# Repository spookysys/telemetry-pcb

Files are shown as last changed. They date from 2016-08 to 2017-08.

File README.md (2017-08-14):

# A brain for my rocket

## Features 

* Arduino-compatible
* Adafruit Feather M0 firmware and pinout
* Small size - fits the smallest model rockets (e.g. 26mm diameter)
* Fairly powerful MCU (Atmel ARM M0 at 32MHz)
* GSM/GPRS for telemetry (SIM868)
* GPS for positioning (SIM868)
* 9-DOF Inertial Motion Unit (MPU-9259)
* Altimeter (BMP-280)
* MicroSD for logging
* Integrated usb-port, lipo-charger and power switch

## Adafruit Feather compatibility

* Same pinout as Adafruit Feather M0. An on-board component interfers with D5 (see note).
* MicroSD wired similar to Adalogger M0, but chip-select is on D7 not D4
* Voltage is 3.0 instead of 3.3
* I2C pull-ups are present

Note: If you don't need hardware handshaking on the GSM UART, the D5 pin can be freed up by cutting JP2 on the back of the board.

## Status

Testing in progress

## Credit

Design derived from Adafruit M0 Feather Proto and Adalogger

Adafruit invests time and resources providing this open source design, 
please support Adafruit and open-source hardware by purchasing 
products from Adafruit!

Creative Commons Attribution, Share-Alike license, check license.txt for more information
All text above must be included in any redistribution

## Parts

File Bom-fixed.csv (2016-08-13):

Part/Designator | Manufacture Part Number/Seeed SKU | Quantity
C12 | 302010001 | 1
C2, C4 | 302010143 | 2
C15 | 302010000 | 1
C10 | 302010006 | 1
C9,C11,C13,C19,C22,C24 | 302010037 | 6
C1,C7,C14 | 302010139 | 3
C3,C5,C6,C8,C17,C20,C21,C23 | 302010103 | 8
C16,C18 | 302020015 | 2
GPS_ANT,GSM_ANT | 320110048 | 2
L1 | 304090046 | 1
L2 | 304090057 | 1
L3 | 304090061 | 1
R2,R6,R7 | 301010291 | 3
R8 | 301010293 | 1
R4, R5 | 301010010 | 2
R1 | 301010089 | 1
R3, R9 | 301010456 | 2
SW1 | 311020047 | 1
X1 | 320110026 | 1
X2 | 306010055 | 1
X3 | 320010000 | 1
D1 | 304020034 | 1
D2 | MMSZ5231BT1G | 1
D3 | SMF05CT2G | 1
U1 | ATSAMD21G18A-M | 1
U2 | SPX3819M5-L-3-0 | 1
U3 | MCP73831T-2ACI/OT | 1
U4 | MPU-9250 | 1
U5 | SIM868 | 1
X4 | 104239-1430 | 1
U6 | BMP280 | 1

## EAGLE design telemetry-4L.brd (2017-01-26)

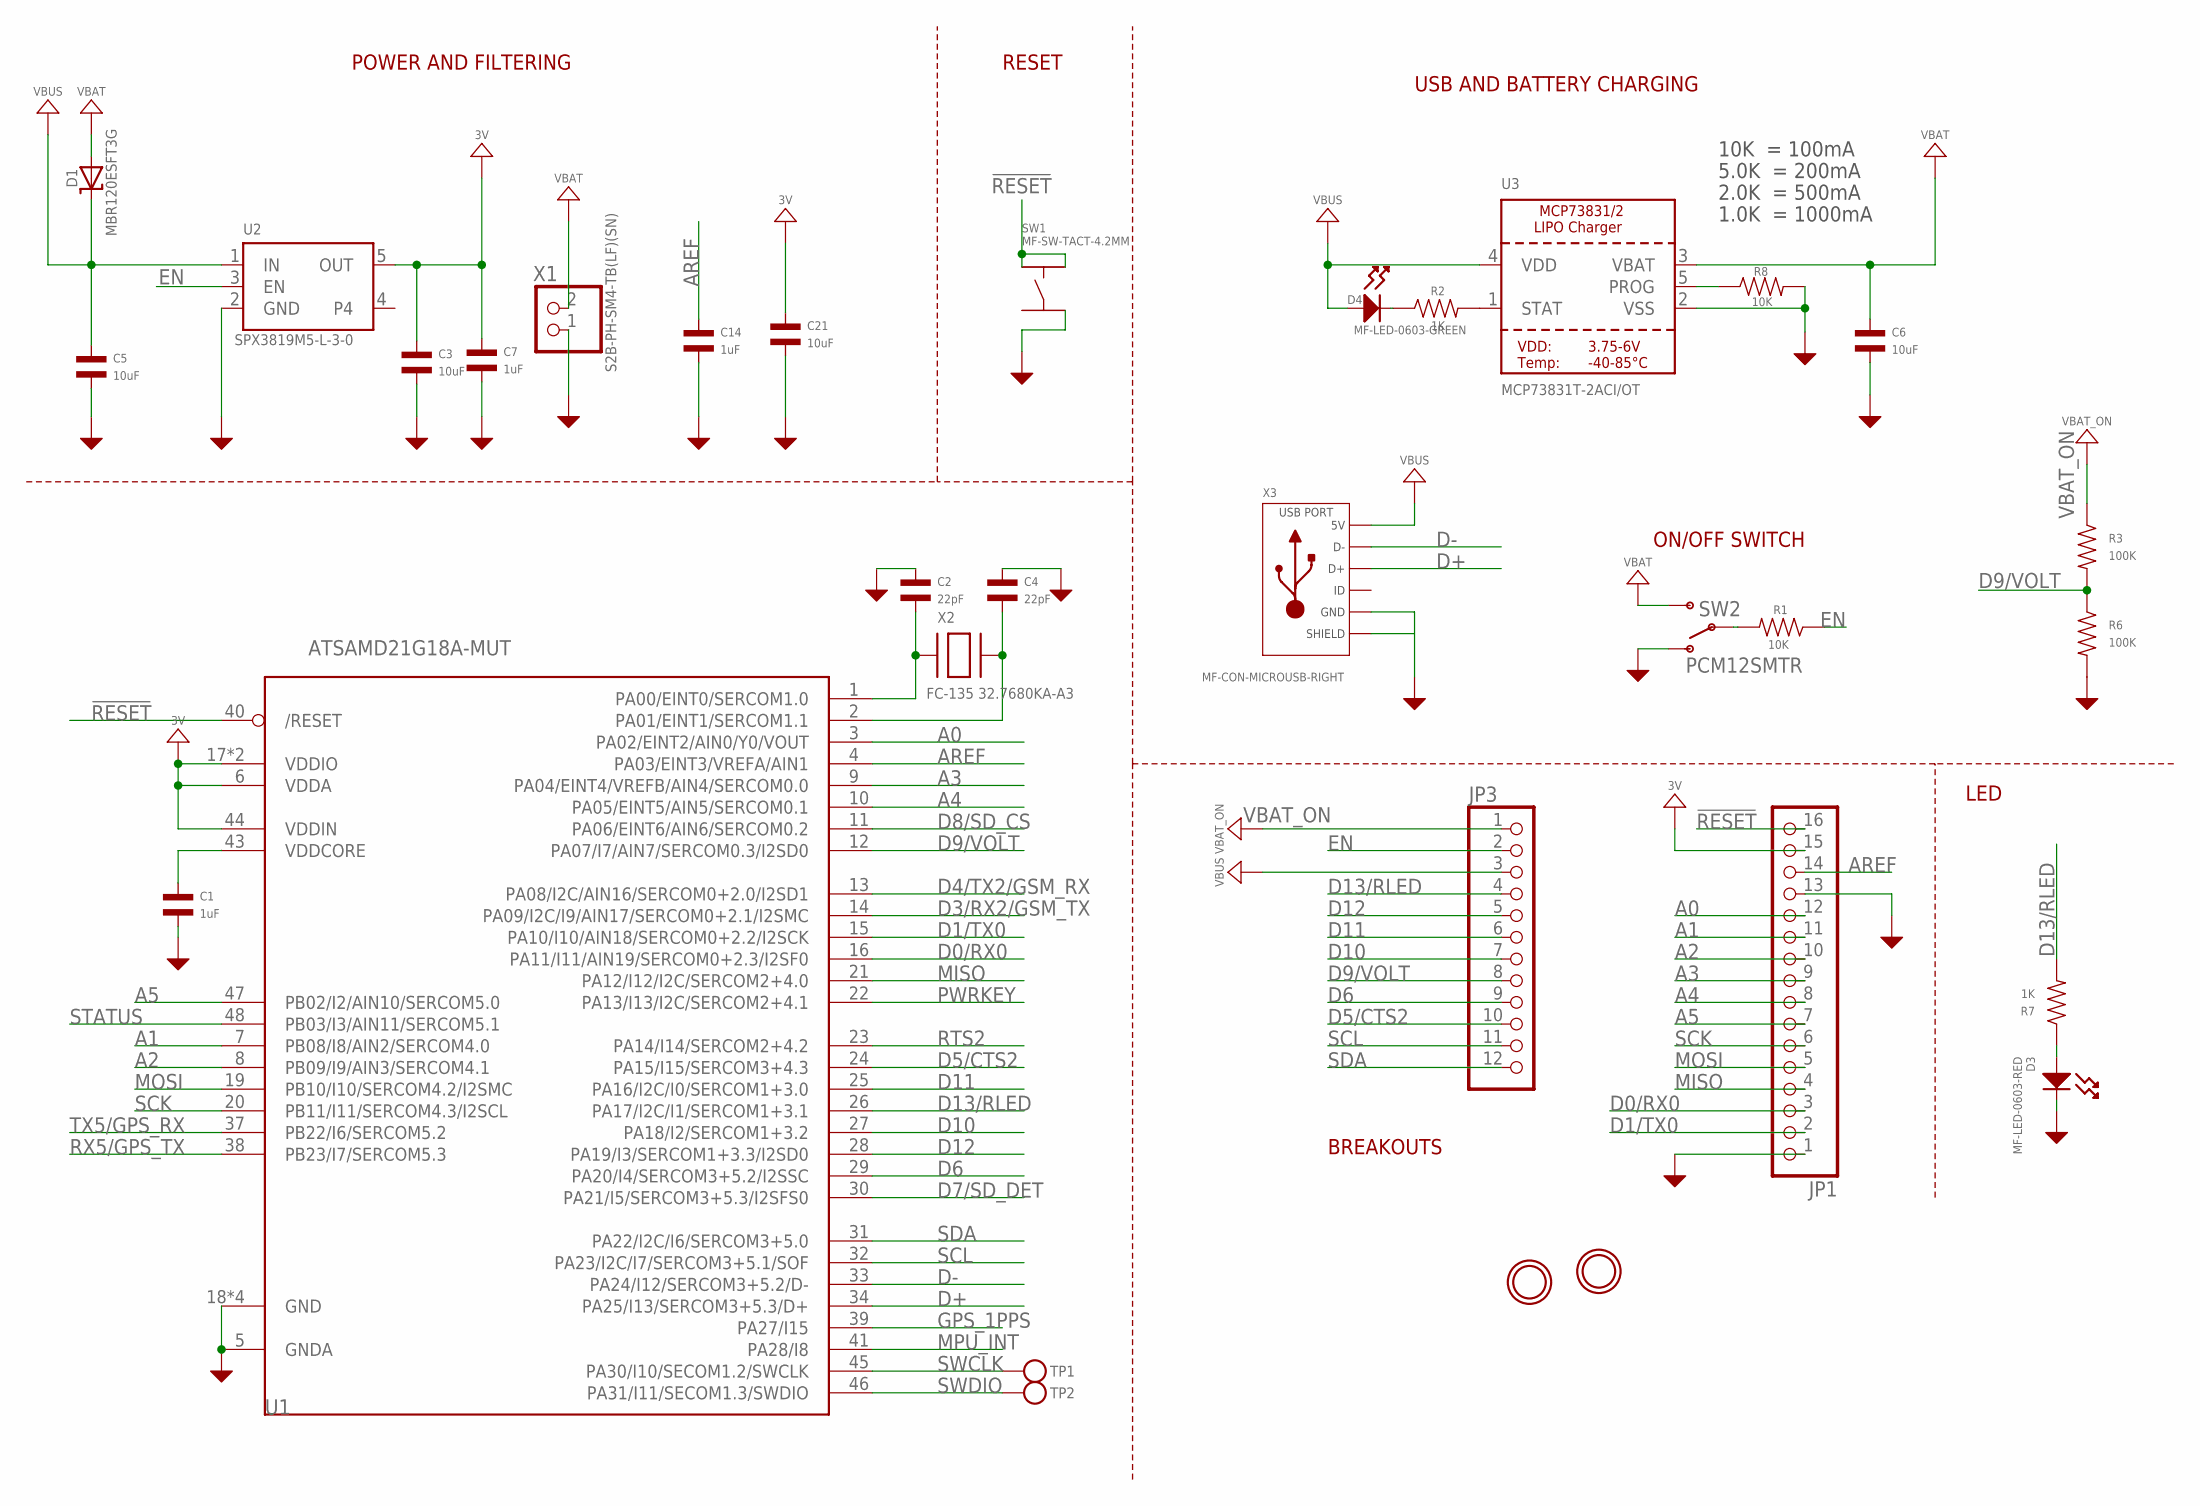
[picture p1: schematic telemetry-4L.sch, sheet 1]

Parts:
C1, C7, C14: 1uF; C0402
C2, C4: 22pF; C0402
C3, C5, C6, C21: 10uF; C0603; MPN GRM188R60J106ME47D
D1: MBR120ESFT3G; SOD-123
D3: MF-LED-0603-RED; LED0603
D4: MF-LED-0603-GREEN; LED0603
JP1: HEADER-1X16ROUND; 1X16_ROUND
JP3: HEADER-1X12; 1X12_ROUND
R1, R8: 10K; R0402
R2, R7: 1K; R0402
R3, R6: 100K; R0402
SW1: MF-SW-TACT-4.2MM; TACT4.2MM
SW2: PCM12SMTR; KPS-1290
TP1, TP2: TESTPOINTROUND1.5MM; TESTPOINT_ROUND_1.5MM
U1: ATSAMD21G18A-MUT; TQFN48_7MM
U2: SPX3819M5-L-3-0; SOT23-5
U3: MCP73831T-2ACI/OT; SOT23-5
U$31, U$32: MOUNTINGHOLE2.5; MOUNTINGHOLE_2.5_PLATED
X1: S2B-PH-SM4-TB(LF)(SN); JSTPH2
X2: FC-135 32.7680KA-A3; XTAL3215
X3: MF-CON-MICROUSB-RIGHT; MICROUSB-RIGHT

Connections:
!RESET: JP1.16, SW1.P$1, SW1.P$2, U1.40 (/RESET)
+3V: C3.P$1, C7.P$1, C21.P$1, JP1.15, U1.6 (VDDA), U1.17 (VDDIO), U1.36 (VDDIO), U1.44 (VDDIN), U2.5 (OUT); also elsewhere on the board
A0: JP1.12, U1.3 (PA02/EINT2/AIN0/Y0/VOUT)
A1: JP1.11, U1.7 (PB08/I8/AIN2/SERCOM4.0)
A2: JP1.10, U1.8 (PB09/I9/AIN3/SERCOM4.1)
A3: JP1.9, U1.9 (PA04/EINT4/VREFB/AIN4/SERCOM0.0)
A4: JP1.8, U1.10 (PA05/EINT5/AIN5/SERCOM0.1)
A5: JP1.7, U1.47 (PB02/I2/AIN10/SERCOM5.0)
AREF: C14.P$1, JP1.14, U1.4 (PA03/EINT3/VREFA/AIN1)
D0/RX0: JP1.3, U1.16 (PA11/I11/AIN19/SERCOM0+2.3/I2SF0)
D1/TX0: JP1.2, U1.15 (PA10/I10/AIN18/SERCOM0+2.2/I2SCK)
D3/RX2/GSM_TX: U1.14 (PA09/I2C/I9/AIN17/SERCOM0+2.1/I2SMC); also elsewhere on the board
D4/TX2/GSM_RX: U1.13 (PA08/I2C/AIN16/SERCOM0+2.0/I2SD1); also elsewhere on the board
D5/CTS2: JP3.10, U1.24 (PA15/I15/SERCOM3+4.3); also elsewhere on the board
D6: JP3.9, U1.29 (PA20/I4/SERCOM3+5.2/I2SSC)
D7/SD_DET: U1.30 (PA21/I5/SERCOM3+5.3/I2SFS0); also elsewhere on the board
D8/SD_CS: U1.11 (PA06/EINT6/AIN6/SERCOM0.2); also elsewhere on the board
D9/VOLT: JP3.8, R3.P$2, R6.P$1, U1.12 (PA07/I7/AIN7/SERCOM0.3/I2SD0)
D10: JP3.7, U1.27 (PA18/I2/SERCOM1+3.2)
D11: JP3.6, U1.25 (PA16/I2C/I0/SERCOM1+3.0)
D12: JP3.5, U1.28 (PA19/I3/SERCOM1+3.3/I2SD0)
D13/RLED: JP3.4, R7.P$2, U1.26 (PA17/I2C/I1/SERCOM1+3.1)
D+: U1.34 (PA25/I13/SERCOM3+5.3/D+), X3.3 (D+)
D-: U1.33 (PA24/I12/SERCOM3+5.2/D-), X3.2 (D-)
EN: JP3.2, R1.P$1, U2.3 (EN); also elsewhere on the board
GND: C1.P$2, C2.P$1, C3.P$2, C4.P$1, C5.P$2, C6.P$2, C7.P$2, C14.P$2, C21.P$2, D3.CATHODE, JP1.1, JP1.13, R6.P$2, R8.P$2, SW1.P$4, SW2.O, U1.5 (GNDA), U1.18 (GND), U1.35 (GND), U1.42 (GND), U1.THERMAL (GND), U2.2 (GND), U3.2 (VSS), X1.1, X3.5 (GND), X3.S1 (SLD), X3.S2 (SLD), X3.S3 (SLD), X3.S4 (SLD), X3.S5 (SLD), X3.S6 (SLD); also elsewhere on the board
GPS_1PPS: U1.39 (PA27/I15); also elsewhere on the board
MISO: JP1.4, U1.21 (PA12/I12/I2C/SERCOM2+4.0); also elsewhere on the board
MOSI: JP1.5, U1.19 (PB10/I10/SERCOM4.2/I2SMC); also elsewhere on the board
MPU_INT: U1.41 (PA28/I8); also elsewhere on the board
unnamed: D4.CATHODE, R2.P$1
unnamed: R2.P$2, U3.1 (STAT)
unnamed: R8.P$1, U3.5 (PROG)
unnamed: C2.P$2, U1.1 (PA00/EINT0/SERCOM1.0), X2.P$1
unnamed: C4.P$2, U1.2 (PA01/EINT1/SERCOM1.1), X2.P$2
unnamed: D3.ANODE, R7.P$1
unnamed: R1.P$2, SW2.P
PWRKEY: U1.22 (PA13/I13/I2C/SERCOM2+4.1); also elsewhere on the board
RTS2: U1.23 (PA14/I14/SERCOM2+4.2); also elsewhere on the board
RX5/GPS_TX: U1.38 (PB23/I7/SERCOM5.3); also elsewhere on the board
SCK: JP1.6, U1.20 (PB11/I11/SERCOM4.3/I2SCL); also elsewhere on the board
SCL: JP3.11, U1.32 (PA23/I2C/I7/SERCOM3+5.1/SOF); also elsewhere on the board
SDA: JP3.12, U1.31 (PA22/I2C/I6/SERCOM3+5.0); also elsewhere on the board
STATUS: U1.48 (PB03/I3/AIN11/SERCOM5.1); also elsewhere on the board
SWCLK: TP1.P$1, U1.45 (PA30/I10/SECOM1.2/SWCLK); also elsewhere on the board
SWDIO: TP2.P$1, U1.46 (PA31/I11/SECOM1.3/SWDIO)
TX5/GPS_RX: U1.37 (PB22/I6/SERCOM5.2); also elsewhere on the board
VBAT: C6.P$1, D1.A, SW2.S, U3.3 (VBAT), X1.2; also elsewhere on the board
VBAT_ON: JP3.1, R3.P$1; also elsewhere on the board
VBUS: C5.P$1, D1.C, D4.ANODE, JP3.3, U2.1 (IN), U3.4 (VDD), X3.1 (5V)
VDDCORE: C1.P$1, U1.43 (VDDCORE)

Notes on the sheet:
POWER AND FILTERING
RESET
10K = 100mA
5.0K = 200mA
2.0K = 500mA
1.0K = 1000mA
USB AND BATTERY CHARGING
BREAKOUTS
LED
ON/OFF SWITCH

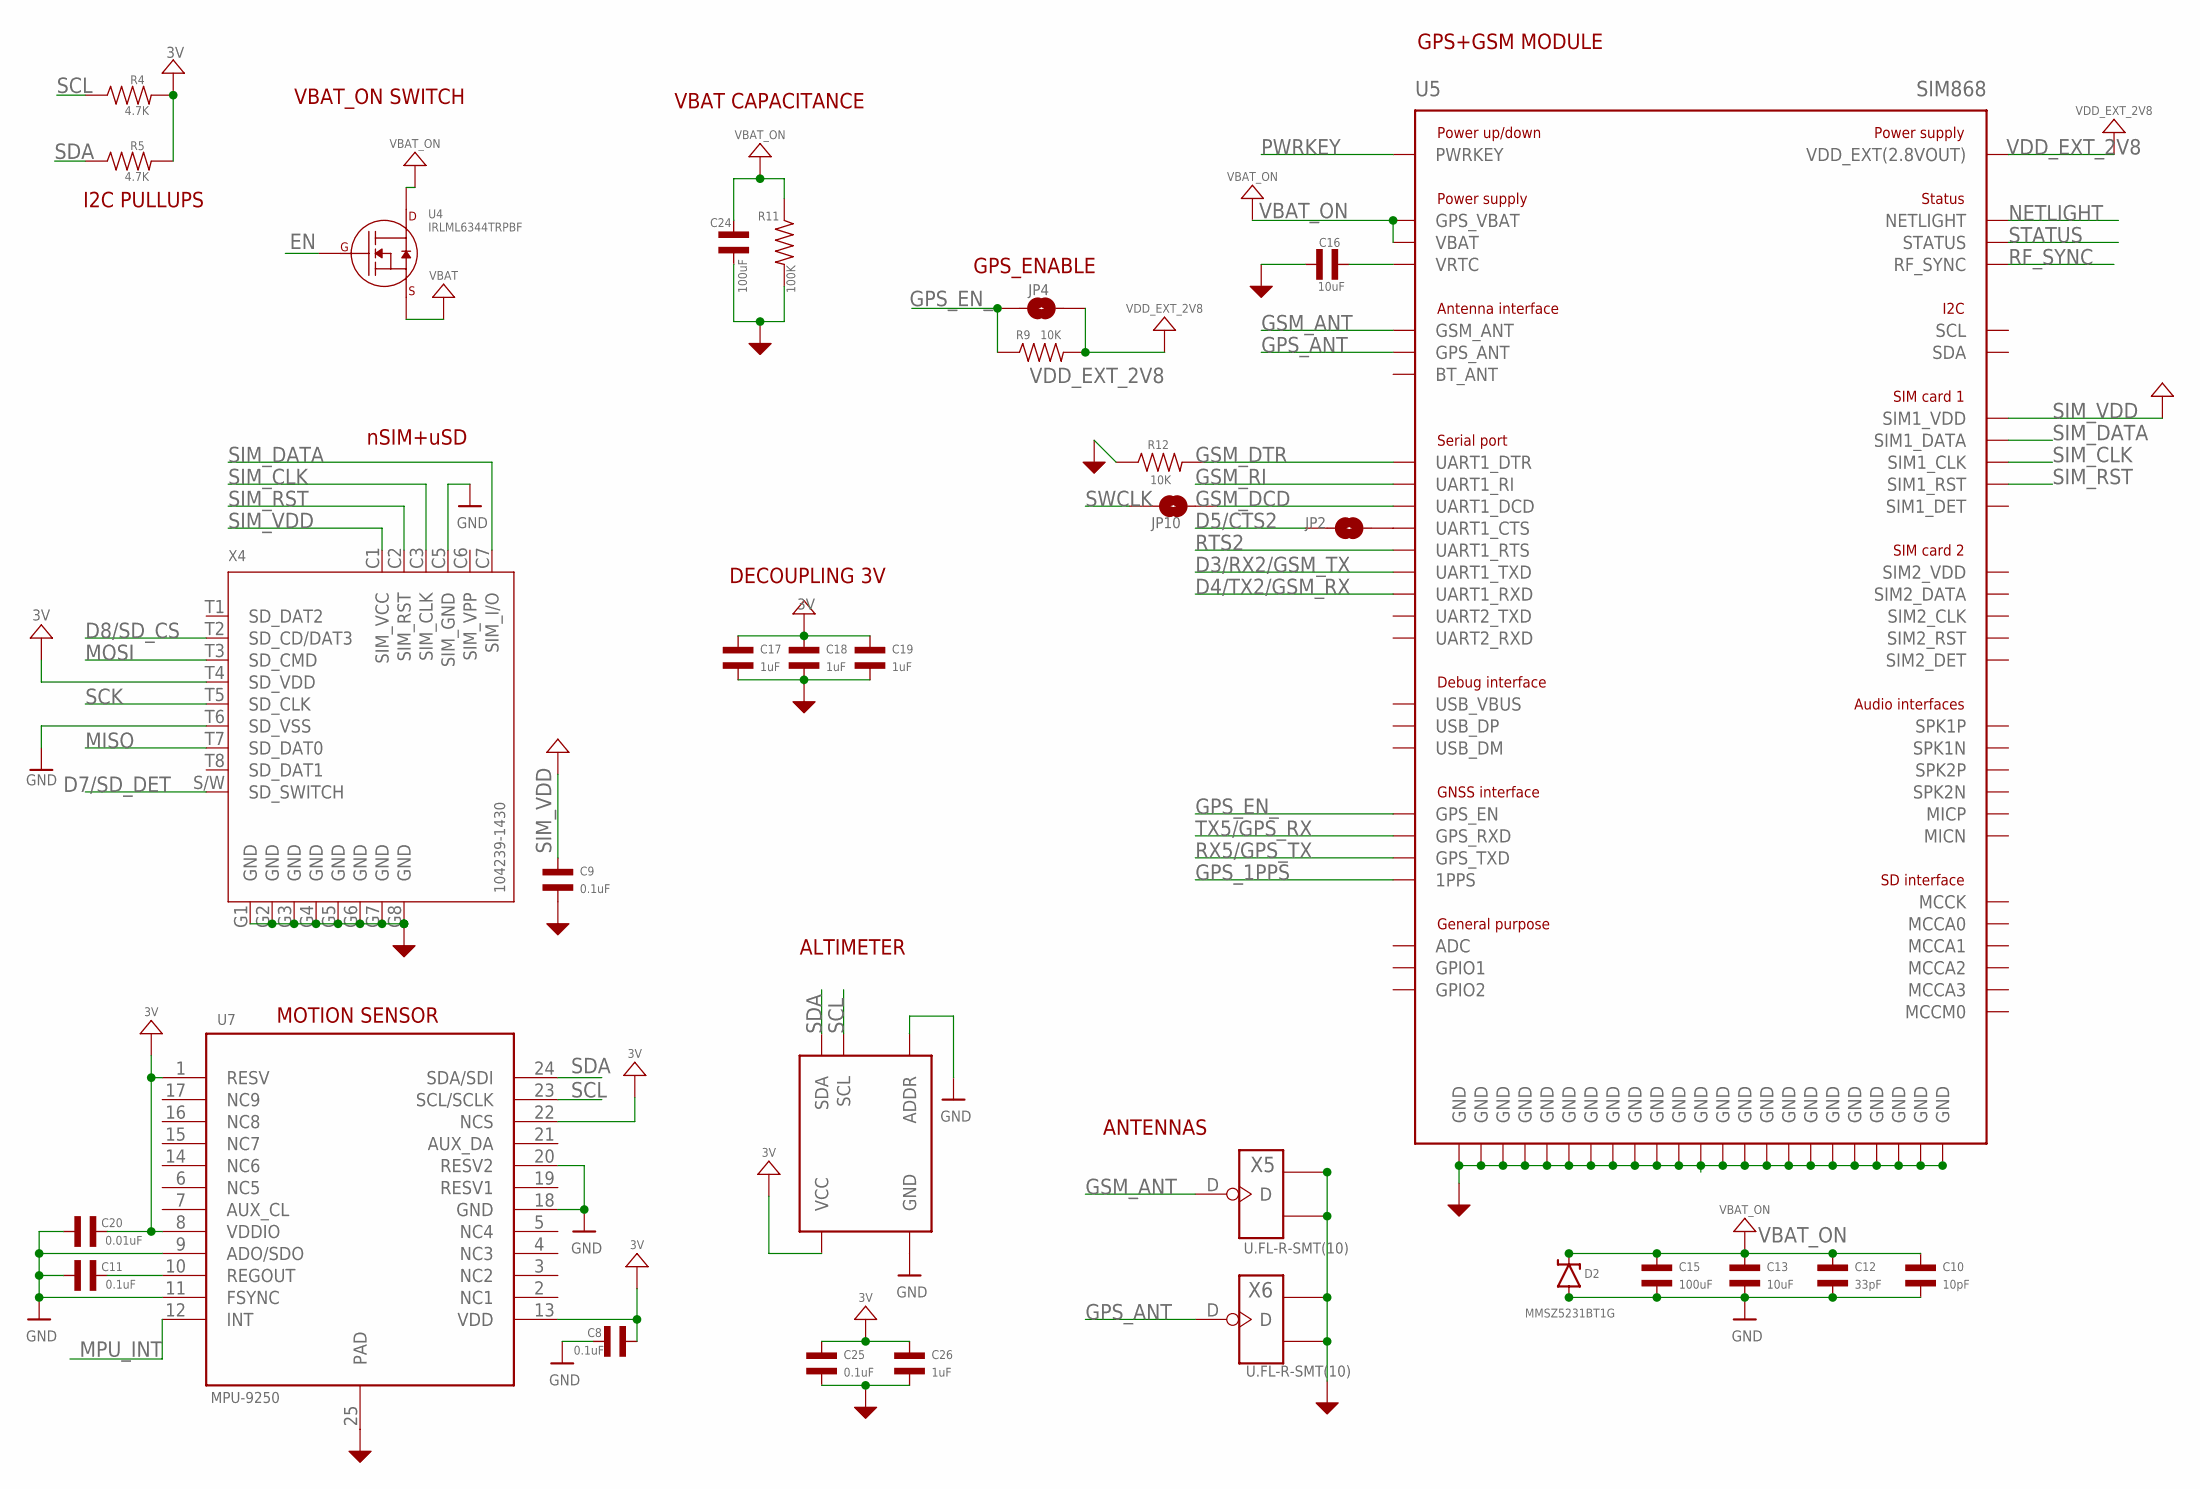
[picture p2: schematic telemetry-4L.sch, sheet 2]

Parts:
C8, C9, C11, C25: 0.1uF; C0402
C10: 10pF; C0402; MPN GRM1555C1H100JA01J
C12: 33pF; C0402; MPN GRM1555C1H330JA01D
C13, C16: 10uF; C0603; MPN GRM188R60J106ME47D
C15, C24: 100uF; C1206; MPN CL31A107MQHNNNE
C17, C18, C19, C26: 1uF; C0402
C20: 0.01uF; C0402
D2: MMSZ5231BT1G; SOD-123
JP2, JP4, JP10: JUMPER-PAD-2-NOYES_SILK; PAD-JUMPER-2-NO_YES_SILK
R4, R5: 4.7K; R0402
R9, R12: 10K; R0402
R11: 100K; R0402
U4: IRLML6344TRPBF; SOT-23-3
U5: SIM868; MPN SIM868
U6: BMP280; LGA-8
U7: MPU-9250; LEAD-QFN24
X4: 104239-1430; MOLEX-SD+SIM-104239; MPN 104239-1430
X5, X6: U.FL-R-SMT(10); U-FL3P-SMD-2.6X2.6X1.0MM

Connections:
+3V: C8.P$2, C17.P$1, C18.P$1, C19.P$1, C20.P$2, C25.P$1, C26.P$1, R4.P$2, R5.P$2, U6.P2 (VCC), U6.P6 (VCC), U6.P8 (VCC), U7.1 (RESV), U7.8 (VDDIO), U7.13 (VDD), U7.22 (NCS), X4.T4 (SD_VDD); also elsewhere on the board
D3/RX2/GSM_TX: U5.1_ (UART1_TXD); also elsewhere on the board
D4/TX2/GSM_RX: U5.2_ (UART1_RXD); also elsewhere on the board
D5/CTS2: JP2.1; also elsewhere on the board
D7/SD_DET: X4.S/W (SD_SWITCH); also elsewhere on the board
D8/SD_CS: X4.T2 (SD_CD/DAT3); also elsewhere on the board
EN: U4.P$1 (GATE); also elsewhere on the board
GND: C8.P$1, C9.P$2, C10.P$2, C11.P$1, C12.P$2, C13.P$2, C15.P$2, C16.P$1, C17.P$2, C18.P$2, C19.P$2, C20.P$1, C24.P$2, C25.P$2, C26.P$2, D2.A, R11.P$2, R12.P$1, U5.8_ (GND), U5.13_ (GND), U5.19_ (GND), U5.21_ (GND), U5.27_ (GND), U5.30_ (GND), U5.31_ (GND), U5.33_ (GND), U5.36_ (GND), U5.37_ (GND), U5.45_ (GND), U5.63_ (GND), U5.66_ (GND), U5.67_ (GND), U5.69_ (GND), U5.70_ (GND), U5.71_ (GND), U5.72_ (GND), U5.73_ (GND), U5.74_ (GND), U5.75_ (GND), U5.76_ (GND), U5.77_ (GND), U6.P1 (GND), U6.P5 (ADDR), U6.P7 (GND), U7.9 (ADO/SDO), U7.11 (FSYNC), U7.18 (GND), U7.20 (RESV2), U7.25 (PAD), X4.C5 (SIM_GND), X4.G1 (GND), X4.G2 (GND), X4.G3 (GND), X4.G4 (GND), X4.G5 (GND), X4.G6 (GND), X4.G7 (GND), X4.G8 (GND), X4.T6 (SD_VSS), X5.GND1, X5.GND2, X6.GND1, X6.GND2; also elsewhere on the board
GPS_1PPS: U5.60_ (1PPS); also elsewhere on the board
GPS_ANT: U5.68_ (GPS_ANT), X6.D
GPS_EN_: JP4.1, R9.P$1, U5.59_ (GPS_EN)
GSM_ANT: U5.32_ (GSM_ANT), X5.D
GSM_DCD: JP10.2, U5.5_ (UART1_DCD)
GSM_DTR: R12.P$2, U5.6_ (UART1_DTR)
GSM_RI: U5.7_ (UART1_RI)
MISO: X4.T7 (SD_DAT0); also elsewhere on the board
MOSI: X4.T3 (SD_CMD); also elsewhere on the board
MPU_INT: U7.12 (INT); also elsewhere on the board
unnamed: JP2.2, U5.4_ (UART1_CTS)
unnamed: C11.P$2, U7.10 (REGOUT)
unnamed: C16.P$2, U5.28_ (VRTC)
NETLIGHT: U5.41_ (NETLIGHT)
PWRKEY: U5.39_ (PWRKEY); also elsewhere on the board
RF_SYNC: U5.29_ (RF_SYNC)
RTS2: U5.3_ (UART1_RTS); also elsewhere on the board
RX5/GPS_TX: U5.61_ (GPS_TXD); also elsewhere on the board
SCK: X4.T5 (SD_CLK); also elsewhere on the board
SCL: R4.P$1, U6.P4 (SCL), U7.23 (SCL/SCLK); also elsewhere on the board
SDA: R5.P$1, U6.P3 (SDA), U7.24 (SDA/SDI); also elsewhere on the board
SIM2_VDD: U5.56_ (SIM2_VDD)
SIM_CLK: U5.16_ (SIM1_CLK), X4.C3 (SIM_CLK)
SIM_DATA: U5.15_ (SIM1_DATA), X4.C7 (SIM_I/O)
SIM_RST: U5.17_ (SIM1_RST), X4.C2 (SIM_RST)
SIM_VDD: C9.P$1, U5.18_ (SIM1_VDD), X4.C1 (SIM_VCC)
STATUS: U5.42_ (STATUS); also elsewhere on the board
SWCLK: JP10.1; also elsewhere on the board
TX5/GPS_RX: U5.62_ (GPS_RXD); also elsewhere on the board
USB_VBUS: U5.24_ (USB_VBUS)
VBAT: U4.P$2 (SOURCE); also elsewhere on the board
VBAT_ON: C10.P$1, C12.P$1, C13.P$1, C15.P$1, C24.P$1, D2.C, R11.P$1, U4.P$3 (DRAIN), U5.34_ (GPS_VBAT), U5.35_ (VBAT); also elsewhere on the board
VDD_EXT_2V8: JP4.2, R9.P$2, U5.40_ (VDD_EXT(2.8VOUT))

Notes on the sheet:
ALTIMETER
nSIM+uSD
I2C PULLUPS
GPS+GSM MODULE
ANTENNAS
GPS_ENABLE
VBAT_ON SWITCH
DECOUPLING 3V
MOTION SENSOR
VBAT CAPACITANCE

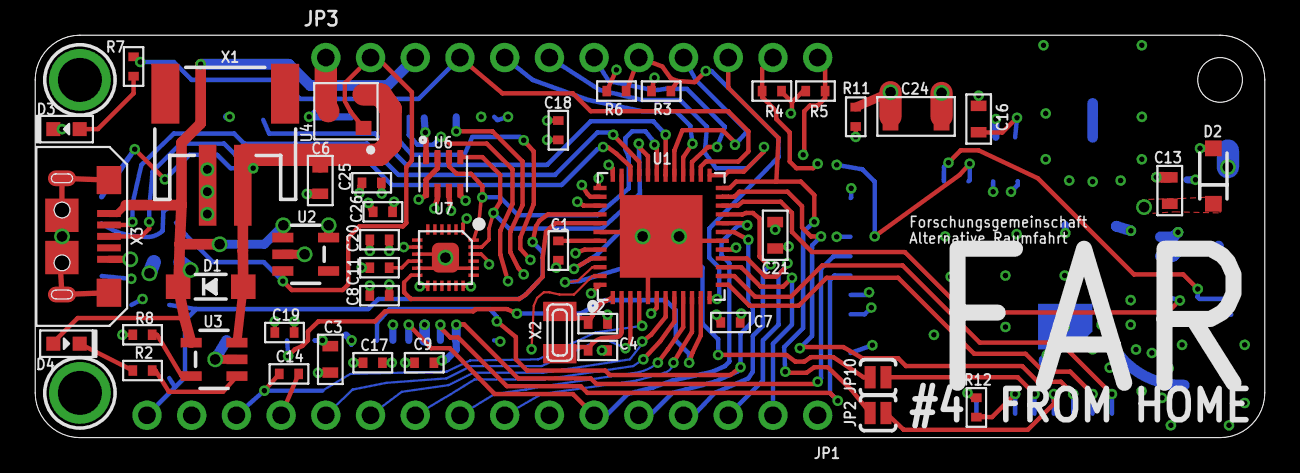
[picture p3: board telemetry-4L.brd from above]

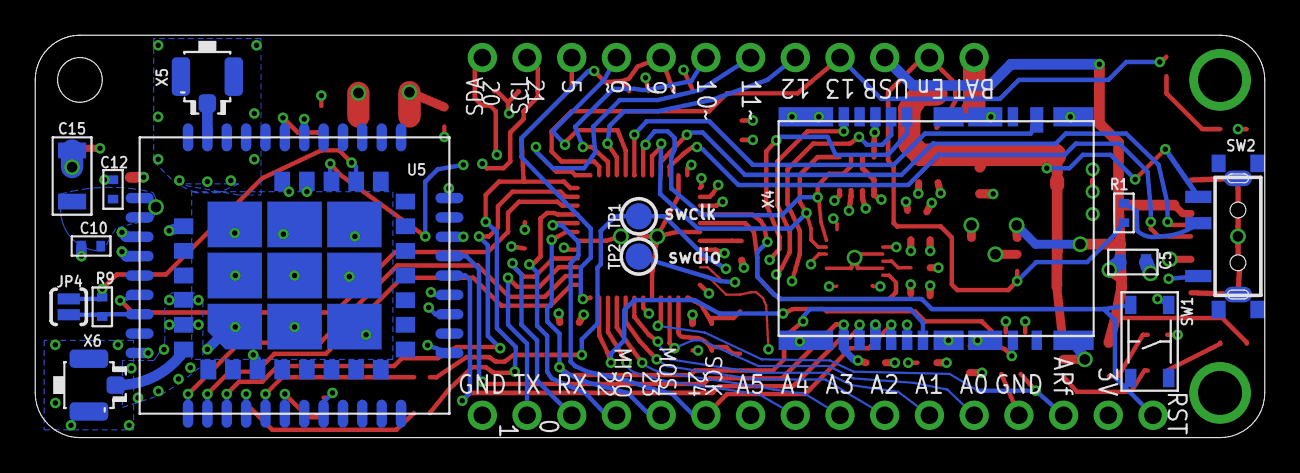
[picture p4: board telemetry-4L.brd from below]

Board: 4 copper layers, 69.8 x 22.9 mm, 63 parts (15 on the bottom side), 64 nets.

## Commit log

2016-08-12 First version i Please enter the commit message for your changes. Lines starting
    [Avionics868.brd, Avionics868.sch]
2016-08-12 Fixed unconnected microsd chip-select
    [Avionics868.brd, Avionics868.sch]
2016-08-12 Prev. commit was faulty, only half fixed Also fixed a number of ERC/DRC issues
    [Avionics868.brd, Avionics868.sch]
2016-08-12 Placed pad for SD_DET
    [Avionics868.brd]
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2016-08-13 Added bypass capacitors ++
    [Avionics868.brd, Avionics868.sch]
2016-08-13 More bypass for SIM and SD
    [Avionics868.brd, Avionics868.sch]
2016-08-13 Removed bRestrict pads from SD/SIM connector
    [Avionics868.brd, Avionics868.sch]
2016-08-13 Changed LEDs to Seeed ++
    [Avionics868.brd, Avionics868.sch]
2016-08-13 Swapped switch for Seeed version
    [Avionics868.brd, Avionics868.sch]
2016-08-13 Swapped Micro-USB connector for Seeed
    [Avionics868.brd, Avionics868.sch]
2016-08-13 Swapped some capacitors
    [Avionics868.brd, Avionics868.sch]
2016-08-13 Added BOM csv file (hand made) for seeed
    [Bom-fixed.csv]
2016-08-13 Swapped obsolete part BMP180 for BMP280
    [Avionics868.brd, Avionics868.sch, Bom-fixed.csv]
2016-08-13 Improved readme, renamed bom-fixed.csv to bom-seeed.csv
    [bom-seeed.csv]
2016-08-13 Aesthetic improvements to placement on backside
    [Avionics868.brd]
2016-08-13 changed all measurements to be in inches
    [Avionics868.brd]
2016-08-13 a ground via was unconnected
    [Avionics868.brd]
2016-08-14 Made lots of tweaks!
    [Avionics868.brd, Avionics868.sch]
2016-08-15 LOTS of tweaks. No more 403s.
    [Avionics868.brd, Avionics868.sch]
2016-08-15 Swapped USB port to deegou
    [Avionics868.brd, Avionics868.sch]
2016-08-15 added seeed MPN as attribute on Deegou USB port
    [Avionics868.brd, Avionics868.sch]
2016-08-15 removed wattages in resistor values
    [Avionics868.brd, Avionics868.sch]
2016-08-15 Did I do anything at all?
    [Avionics868.brd]
2016-08-16 Moved things around to improve capacitor placement
    [Avionics868.brd, Avionics868.sch]
2016-08-16 Added BOM for Deegou Note that bom-seeed is outdated at this point
    [bom-deegou.csv]
2016-08-16 Added some more connections to improve ground covg
    [Avionics868.brd]
2016-08-23 Switched Tantanum AVX-B caps with Ceramic C1206
    [Avionics868.brd, Avionics868.sch]
2016-08-23 killed out of date bom-seed, added some ulps
    [bom-seeed.csv]
2016-08-23 fixed a short circuit introduced when changing the 100uF caps to ceramic
    [Avionics868.brd]
2016-08-23 updated bom-deegou to reflect now using only Ceramic caps
    [bom-deegou.csv]
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2016-09-01 Shrunk the board some mils horizontally
    [Avionics868.brd]
2016-09-01 Made it even a tiny bit shorter
    [Avionics868.brd]
2016-10-07 Tweaked GPS antenna trace
    [Avionics868.brd]
2016-10-08 Added shorter board with some comps on backside
    [telemetry-shorter.brd, telemetry-shorter.sch, telemetry.brd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]
2016-10-08 Small fixes
    [telemetry-shorter.brd, telemetry-shorter.sch]
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2016-10-09 Connected GPS_EN to 2V8 by jumper
    [telemetry-shorter.brd, telemetry-shorter.sch]
2016-10-09 Fixed some DRC failures
    [telemetry-shorter.brd]
2016-10-09 Deleted long board version
    [telemetry.brd, telemetry.sch]
2016-10-09 Added logo to back
    [telemetry-shorter.brd]
2016-10-10 Started new 4-layer version
    [telemetry-4L.brd, telemetry-4L.sch]
2016-10-11 working on new board
    [telemetry-4L.brd]
2016-10-12 Working on 4-layer version
    [telemetry-4L.brd, telemetry-4L.sch]
2016-10-13 Last edit before switching Bosch -> Invensense MPU
    [telemetry-4L.brd]
2016-10-13 Switched to MPU-9250 IMU
    [telemetry-4L.brd, telemetry-4L.sch]
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2016-10-13 Power and ground: routed
    [telemetry-4L.brd]
2016-10-13 Some work on routing
    [telemetry-4L.brd, telemetry-4L.sch]
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2016-10-16 Put Sim868 on backside!
    [telemetry-4L.brd]
2016-10-17 Added a second JP2 socket for servo output
    [telemetry-4L.brd, telemetry-4L.sch]
2016-10-17 Moved power mosfet out
    [telemetry-4L.brd, telemetry-4L.sch]
2016-10-17 Connected servo power in schematic
    [telemetry-4L.brd, telemetry-4L.sch]
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2016-10-18 fixed some names
    [telemetry-4L.brd, telemetry-4L.sch]
2016-10-18 Moved power mosfet back upstream
    [telemetry-4L.brd, telemetry-4L.sch]
2016-10-19 Changed GPS_EN pin to SERVO_EN, so I can arm at a distance
    [telemetry-4L.brd, telemetry-4L.sch]
2016-10-19 Added MPR and POPULATE attributes - didnt seem to do anything though
    [telemetry-4L.brd, telemetry-4L.sch]
2016-10-19 Added a 100uF cap to 5V output
    [telemetry-4L.brd, telemetry-4L.sch]
2016-10-30 Added a pull-down to 5V enable signal
    [telemetry-4L.brd, telemetry-4L.sch]
2016-10-30 fixed some unconnected airwires (important fix)
    [telemetry-4L.brd, telemetry-4L.sch]
2016-10-31 Input capacitor for 5V regulator was wrong value
    [telemetry-4L.brd, telemetry-4L.sch]
2016-10-31 Added wind-down resistor to 5V output Killed cutout under MPU, as I don't know if it will work
    [telemetry-4L.brd, telemetry-4L.sch]
2016-10-31 Made some more space around the 5V supply
    [telemetry-4L.brd]
2016-10-31 added resistor to ground on DTR, as per SIM800 Serial App Note
    [telemetry-4L.brd, telemetry-4L.sch]
2016-11-10 Moved battery connector back a tad, as it got in the way in my current prototype
    [telemetry-4L.brd]
2016-11-12 Moved both power plugs back a tad
    [telemetry-4L.brd]
2016-11-15 Added connection to DCD shared with SWCLK - might be needed for FTP and similar
    Try using FTP and if not needed, kill this again
    [telemetry-4L.brd, telemetry-4L.sch]
2016-11-15 Fixed the PCB to reflect last change in schematic
    [telemetry-4L.brd, telemetry-4L.sch]
2016-11-15 Logo aesthetics - added #2
    [telemetry-4L.brd]
2016-11-15 Fixed a problem with overlapping diode and cleaned up files
    [bom-deegou.csv, telemetry-4L.brd]
2016-11-15 More fixes of overlapping components
    [telemetry-4L.brd, telemetry-4L.sch]
2016-11-23 Connected 1PPS via jumper made CTS jumper default NO
    [telemetry-4L.brd, telemetry-4L.sch]
2016-12-06 Moved "forsch..." to the backside (correctly)
    [telemetry-4L.brd]
2016-12-23 Increased margins in middle part of board
    [telemetry-4L.brd, telemetry-4L.sch]
2016-12-23 Improvements on the right side
    [telemetry-4L.brd]
2016-12-23 Fixed bigger margins on the right side¨ Only left side remains
    [telemetry-4L.brd]
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2016-12-24 fixed more margins Remember: Have a look at A5 trace and via
    [telemetry-4L.brd, telemetry-4L.sch]
2016-12-24 moved sd slot to the left, making more room for a5
    [telemetry-4L.brd, telemetry-4L.sch]
2016-12-24 Finished layout fixed all obvious errors
    [telemetry-4L.brd]
2016-12-25 attempt to put a right angle reset button
    [telemetry-4L.brd, telemetry-4L.sch]
2016-12-25 Revert "attempt to put a right angle reset button"
    This reverts commit 0c88159f70d3469a455fb55c16ca82abb05fa745.
    [telemetry-4L.brd, telemetry-4L.sch]
2016-12-25 small fixes (some very important)
    [telemetry-4L.brd, telemetry-4L.sch]
2016-12-25 Margins around lower antenna
    [telemetry-4L.brd]
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2016-12-25 Dont know, but this went to ccreate an order
    [telemetry-4L.brd]
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2017-01-26 Swapped power FET with the one used by adafruit - Noticed the old one was the wrong way around!!
    [telemetry-4L.brd, telemetry-4L.sch]
2017-01-26 Revert "Swapped power FET with the one used by adafruit"
    This reverts commit fb89b7665746a5f81bf27fb940dbf5a3e6cbfe7e.
    [telemetry-4L.brd, telemetry-4L.sch]
2017-01-26 Swapped Power MOSFET Source and Drain so it's correct
    [telemetry-4L.brd, telemetry-4L.sch]
2017-01-26 Removed 5V power supply. This can be on shield!
    [telemetry-4L.brd, telemetry-4L.sch]
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2017-01-26 Hooked GPS_1PPS to a normal pin, instead of SWDIO
    [telemetry-4L.brd, telemetry-4L.sch]
2017-01-26 Updated libraries - short circuit in usb plug should be gone. Also moved USB and switch a tad to make it stick better
    [telemetry-4L.brd, telemetry-4L.sch]

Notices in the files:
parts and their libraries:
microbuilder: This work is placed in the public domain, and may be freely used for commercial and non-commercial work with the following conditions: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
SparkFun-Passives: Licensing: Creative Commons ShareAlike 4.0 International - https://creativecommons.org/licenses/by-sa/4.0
